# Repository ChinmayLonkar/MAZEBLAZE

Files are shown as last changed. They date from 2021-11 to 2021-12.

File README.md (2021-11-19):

# MAZEBLAZE

This repository contains hardware design files for the MAZEBLAZE Bot.This project is in developement and is not ready for final release.

It uses -
* TRCT5000 IR Sensors for following the lines on the maze 
* TB6612FNG Motor Driver for controlling two N20 motors
* ESP32 for control and perform tasks at high speeds and accuracy

Following are some images of the PCB Design

* Top View
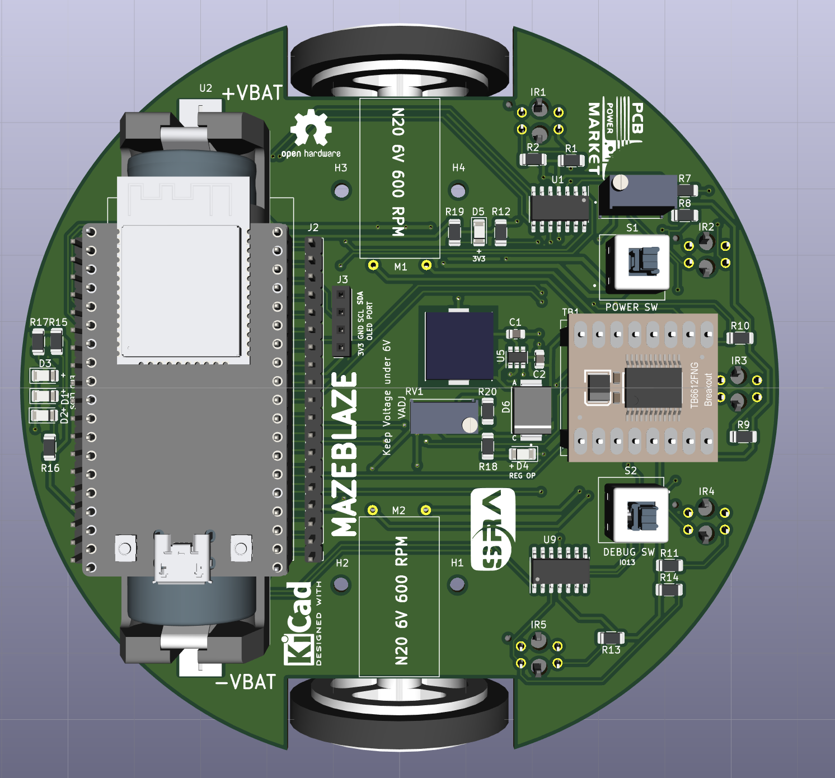
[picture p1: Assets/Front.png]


* Bottom View

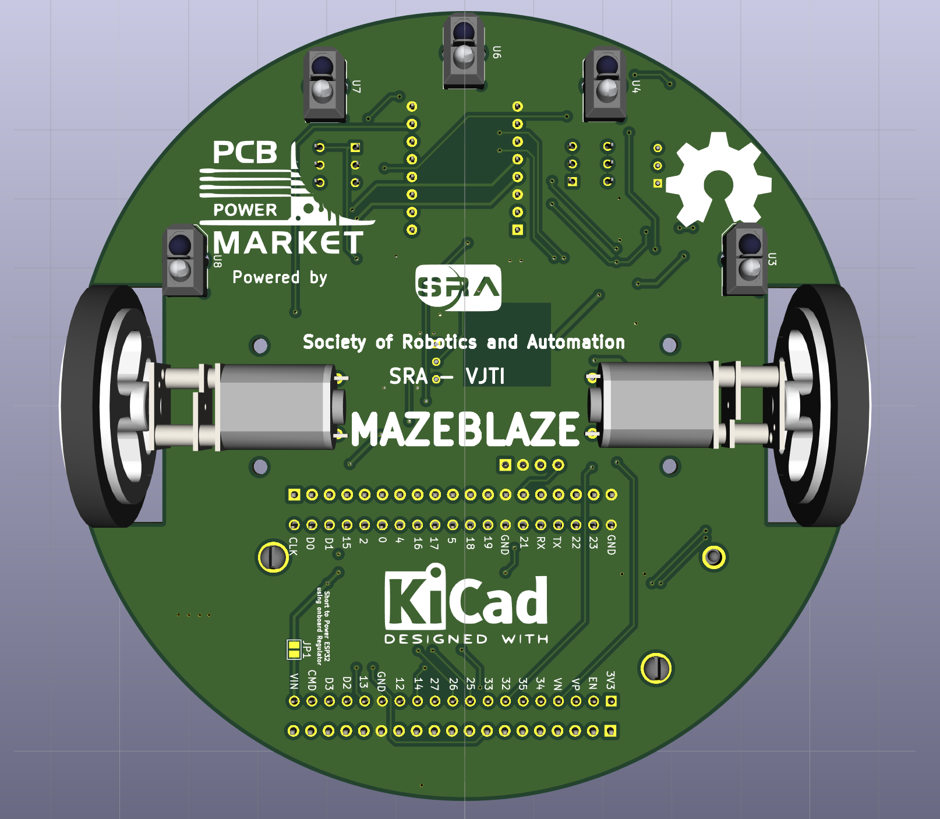
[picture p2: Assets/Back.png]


* Front Copper Layer

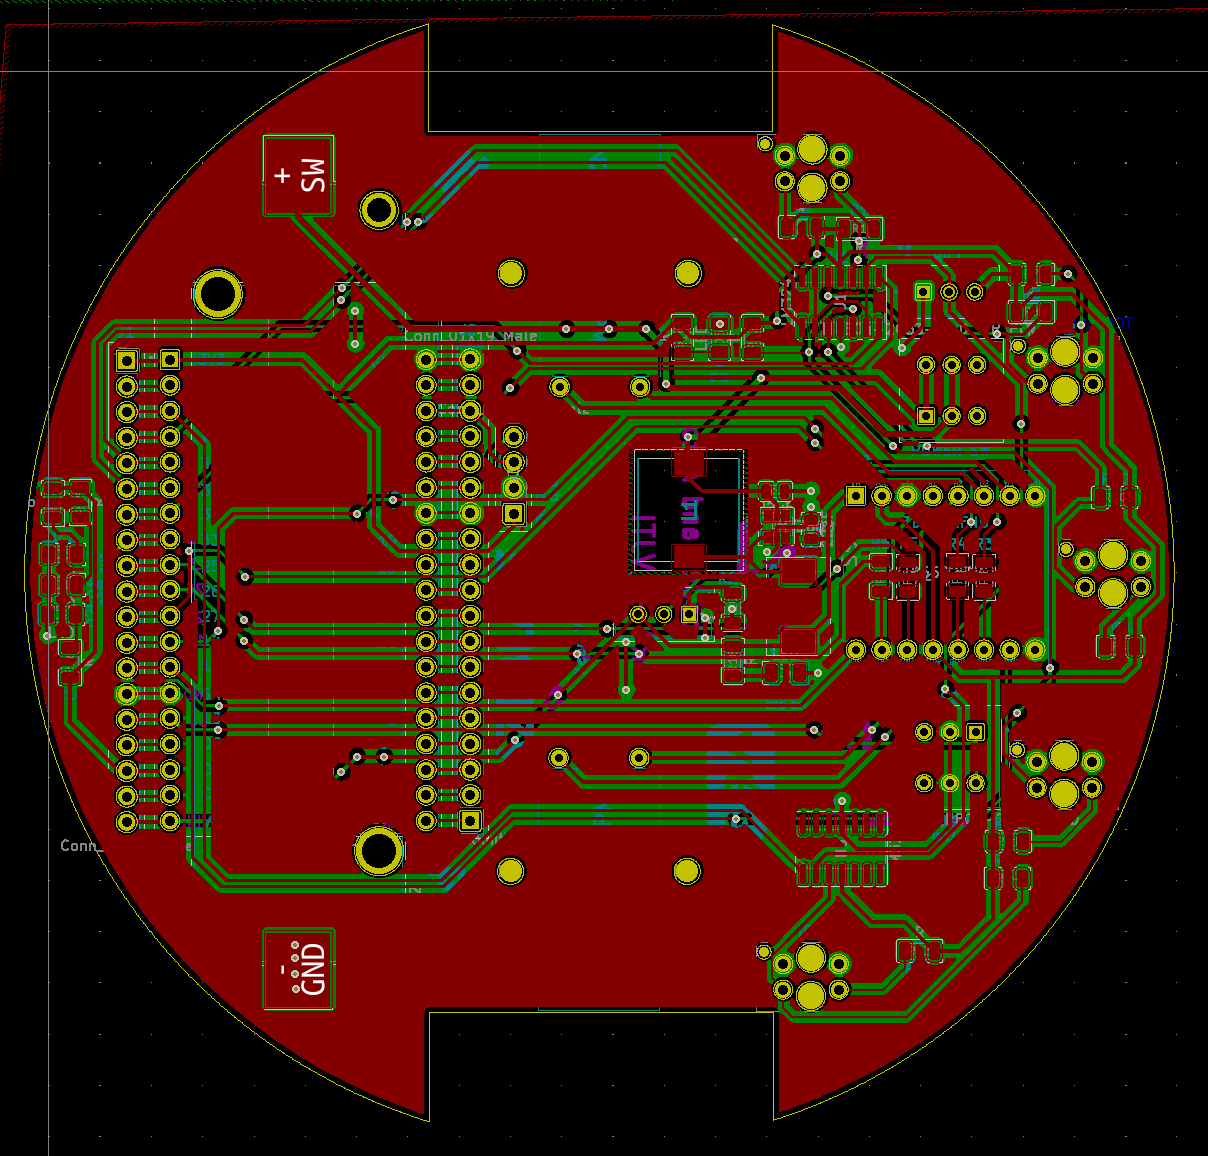
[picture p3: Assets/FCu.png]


* Bottom Copper Layer

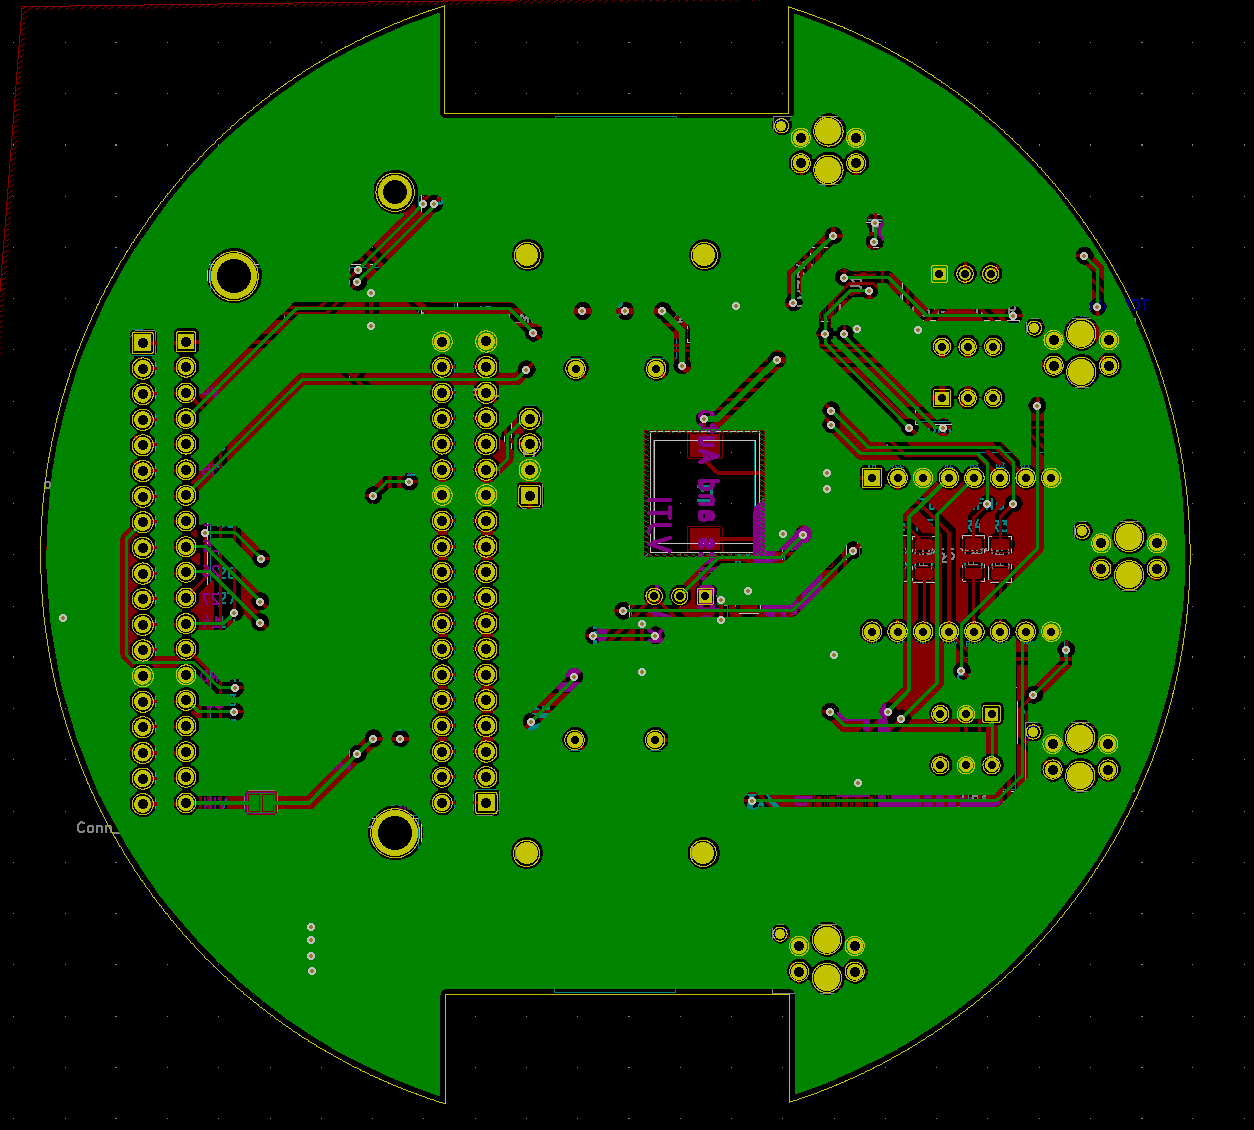
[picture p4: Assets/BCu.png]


* Routing 

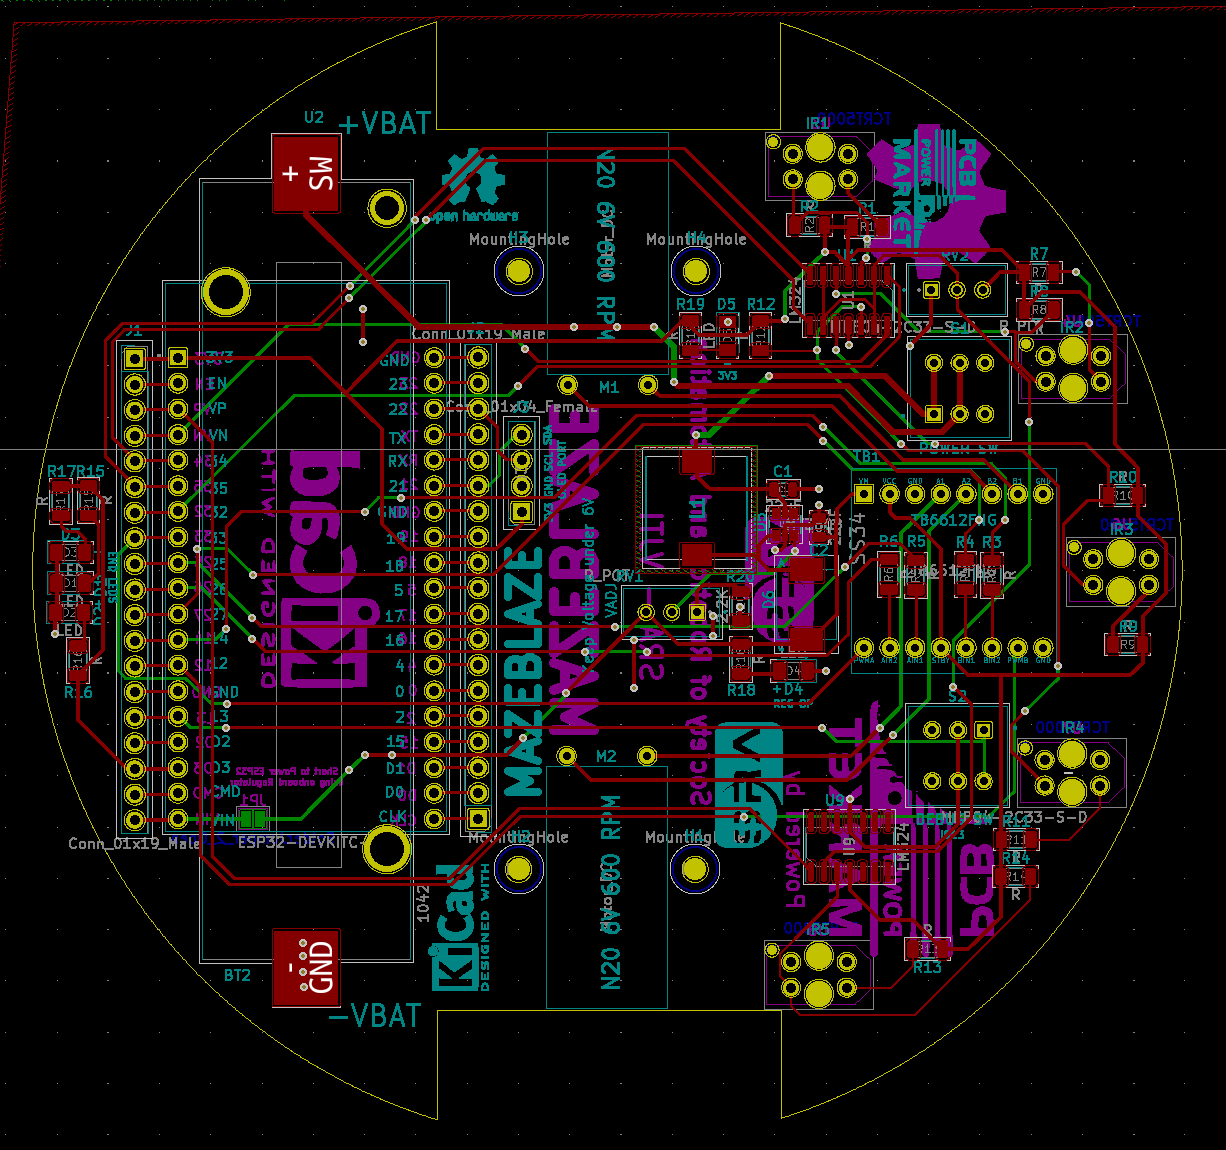
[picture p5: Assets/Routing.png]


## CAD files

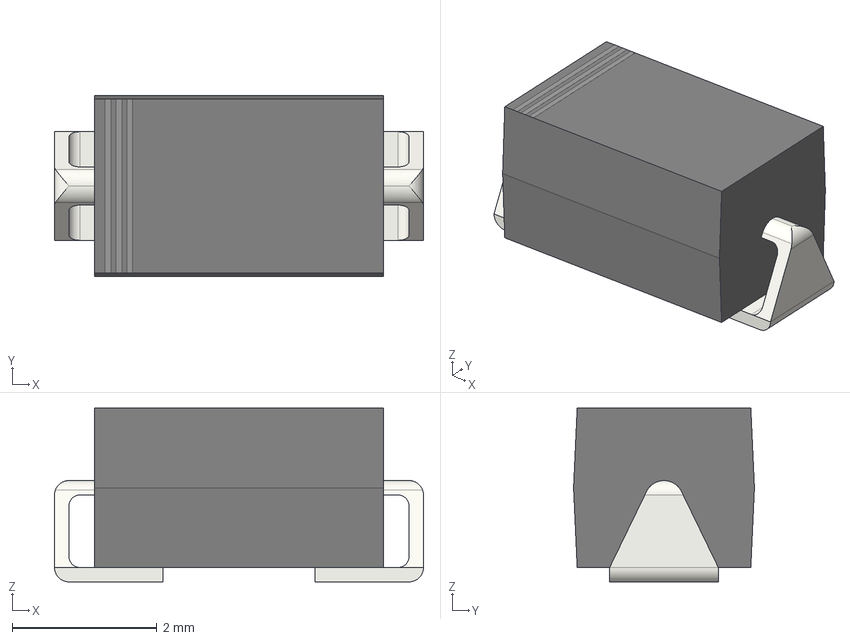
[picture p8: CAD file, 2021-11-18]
pcb_design/3D_Files/SS34.step
5.10 x 2.50 x 2.40 mm

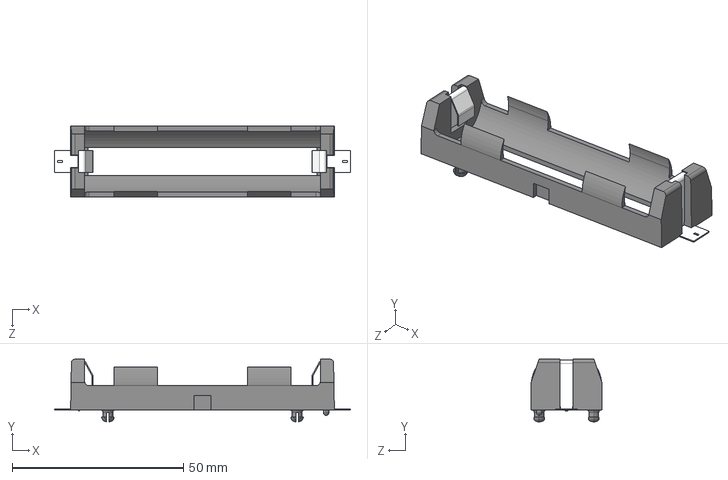
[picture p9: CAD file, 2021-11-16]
pcb_design/Component_libraries/1042/1042.step
86.5 x 18.3 x 20.7 mm

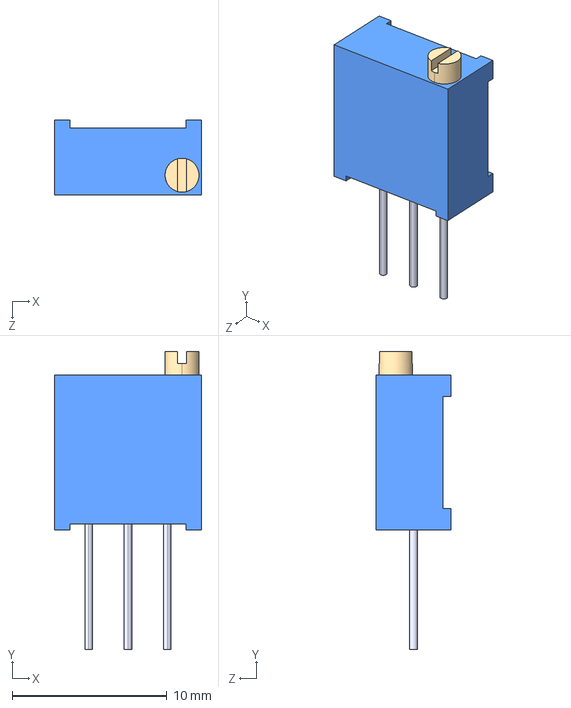
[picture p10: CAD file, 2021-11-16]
pcb_design/Component_libraries/3296W-1-202LF/3296W-1-202LF.step
9.53 x 19.3 x 4.83 mm

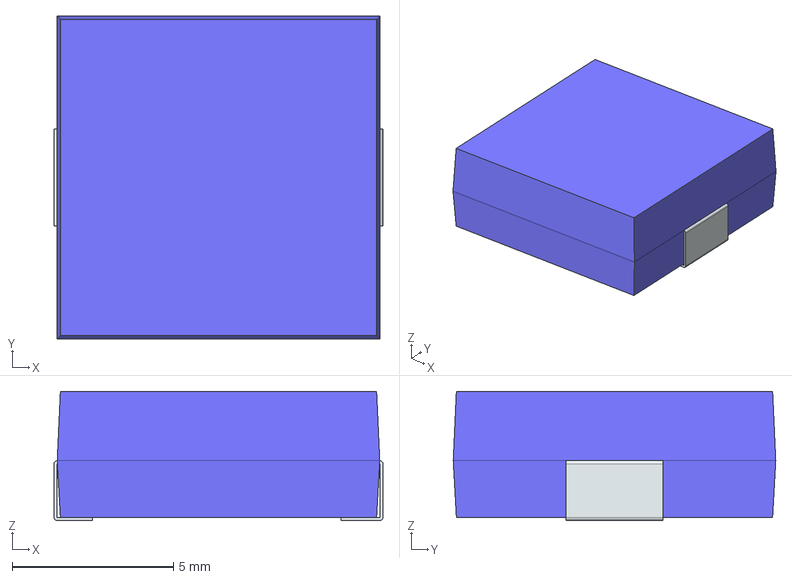
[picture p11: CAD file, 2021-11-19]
pcb_design/Component_libraries/Inductor_CDRH104RNP-220NC/CDRH104RNP-220NC.stp
10.2 x 10.0 x 4.00 mm
FilletPin1
FilletPin2

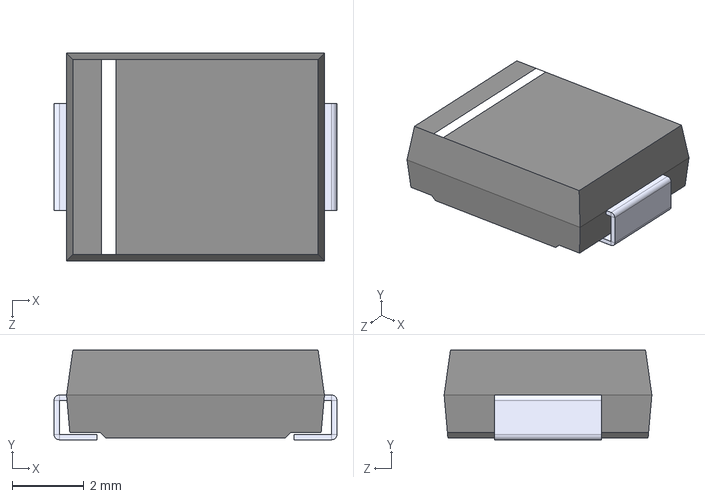
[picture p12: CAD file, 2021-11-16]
pcb_design/Component_libraries/SS34/SS34.step
7.90 x 2.50 x 5.80 mm

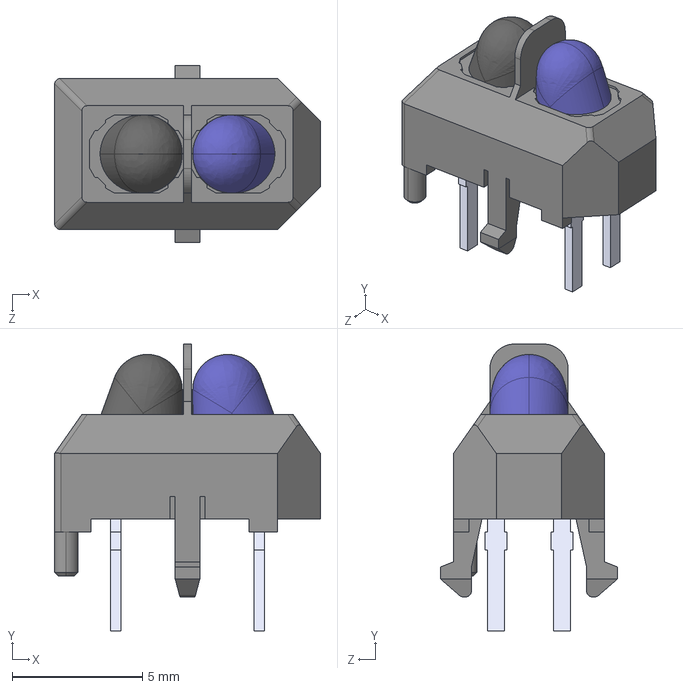
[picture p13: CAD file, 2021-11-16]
pcb_design/Component_libraries/TCRT5000/TCRT5000.step
10.2 x 11.0 x 6.80 mm

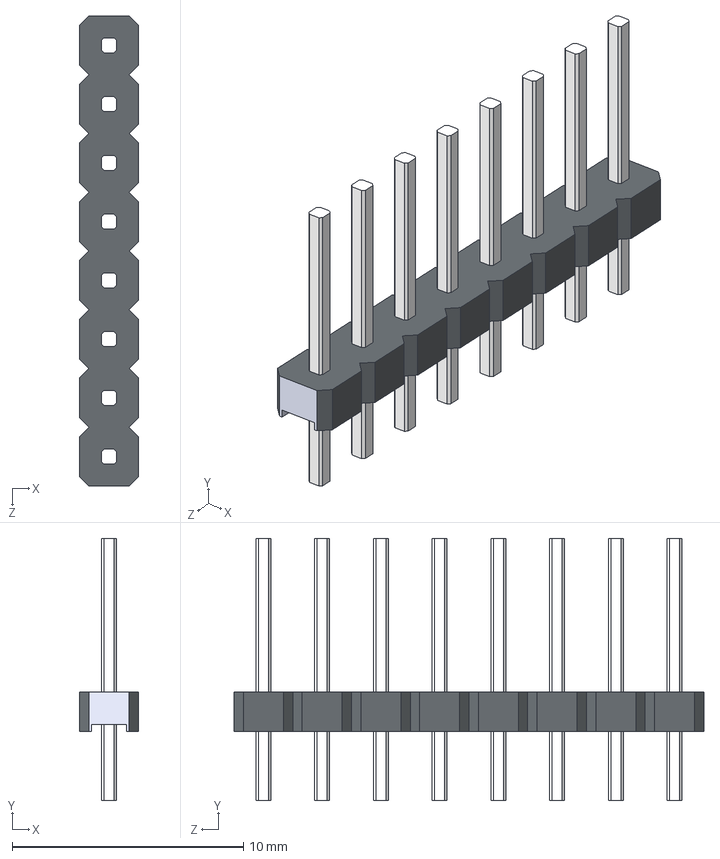
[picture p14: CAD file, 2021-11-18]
pcb_design/3D_Files/1x8.STEP
2.54 x 11.3 x 20.3 mm

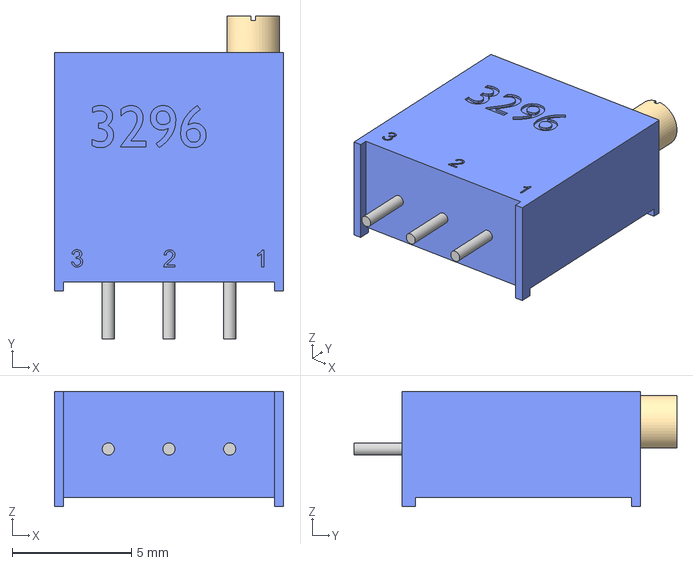
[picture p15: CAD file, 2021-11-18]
pcb_design/3D_Files/Trimpot 3296W.step
9.60 x 13.5 x 4.82 mm

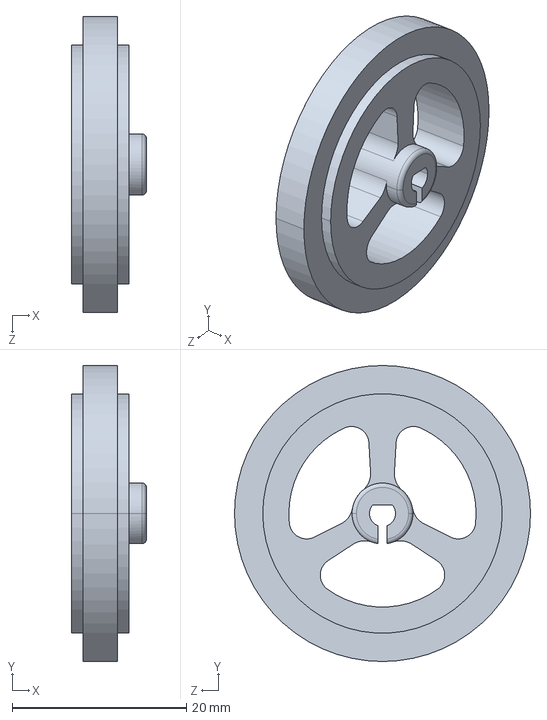
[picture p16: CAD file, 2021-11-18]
pcb_design/3D_Files/Wheel 34 mm.STEP
8.60 x 34.0 x 34.0 mm

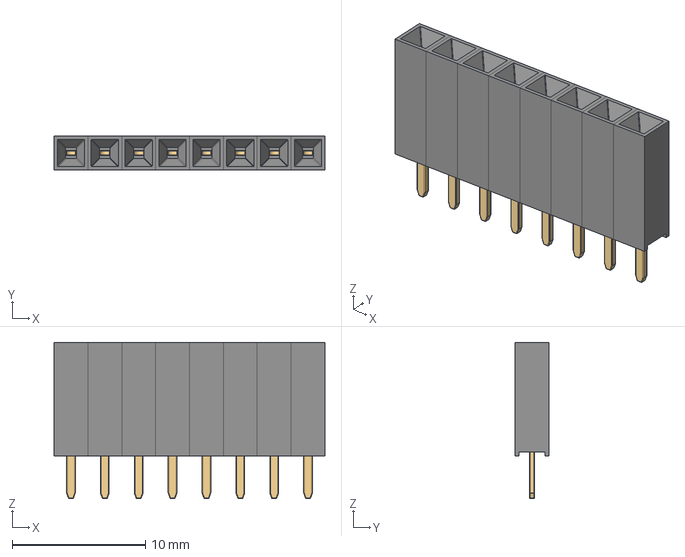
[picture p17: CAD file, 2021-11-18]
pcb_design/3D_Files/Female Pin Header 01x08 Pitch 2.54mm Height 8.5mm.stp
20.3 x 2.54 x 11.7 mm
Female Pin Header 1x x 8

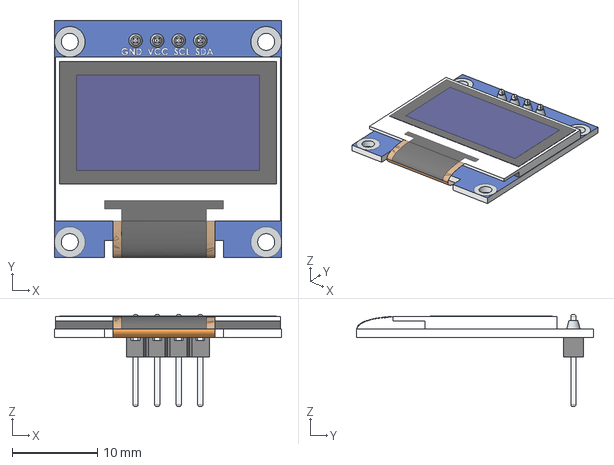
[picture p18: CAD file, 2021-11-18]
pcb_design/3D_Files/OLED-128x64-0.96.step
26.7 x 27.9 x 10.8 mm

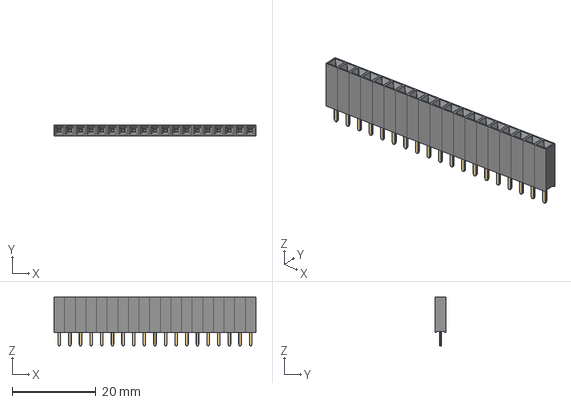
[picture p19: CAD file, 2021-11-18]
pcb_design/3D_Files/Female Pin Header 01x19 Pitch 2.54mm Height 8.5mm.stp
48.3 x 2.54 x 11.7 mm
Female Pin Header 1x x 19

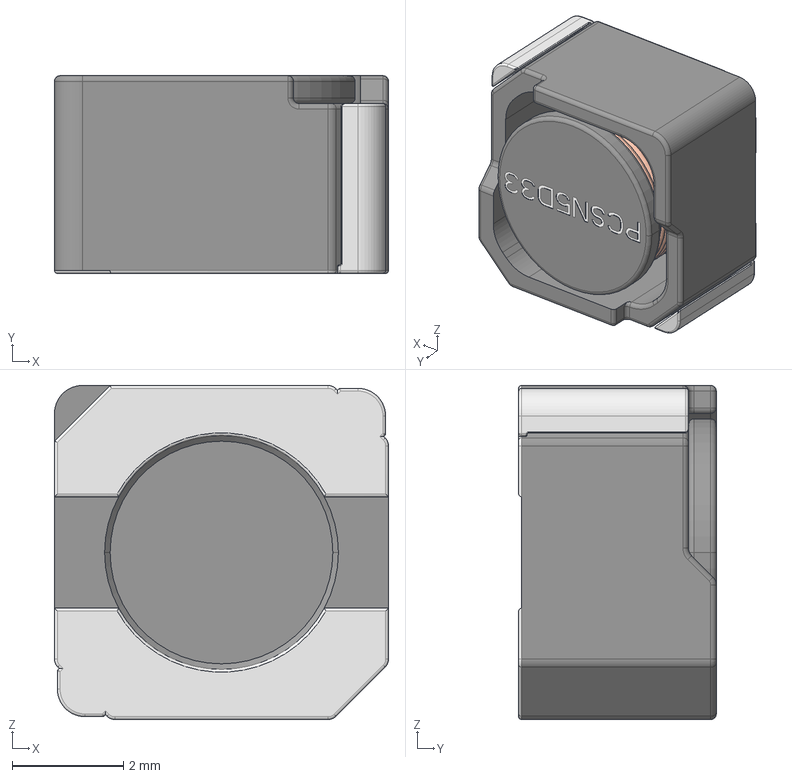
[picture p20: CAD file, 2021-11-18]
pcb_design/3D_Files/pcsn5d33_l6_w6_h3-5.stp
6.00 x 3.55 x 6.00 mm

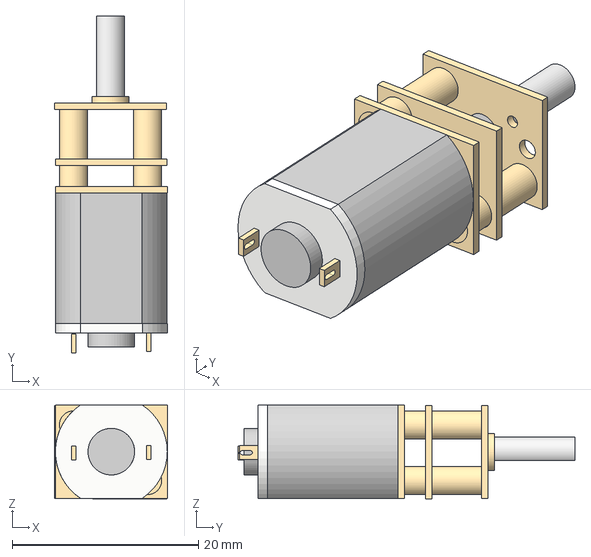
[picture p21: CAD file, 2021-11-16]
pcb_design/3D_Files/MicroGearmotor v3.step
12.1 x 36.1 x 10.1 mm

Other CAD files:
pcb_design/3D_Files/Roda 34 mm.STEP
pcb_design/3D_Files/Push Switch_8x8_6pin_with Lock.stp
pcb_design/3D_Files/18650 _87_89 0=_4.STEP
pcb_design/Component_libraries/Inductor_CDRH104RNP-220NC/CDRH104RNP-220NC.stl

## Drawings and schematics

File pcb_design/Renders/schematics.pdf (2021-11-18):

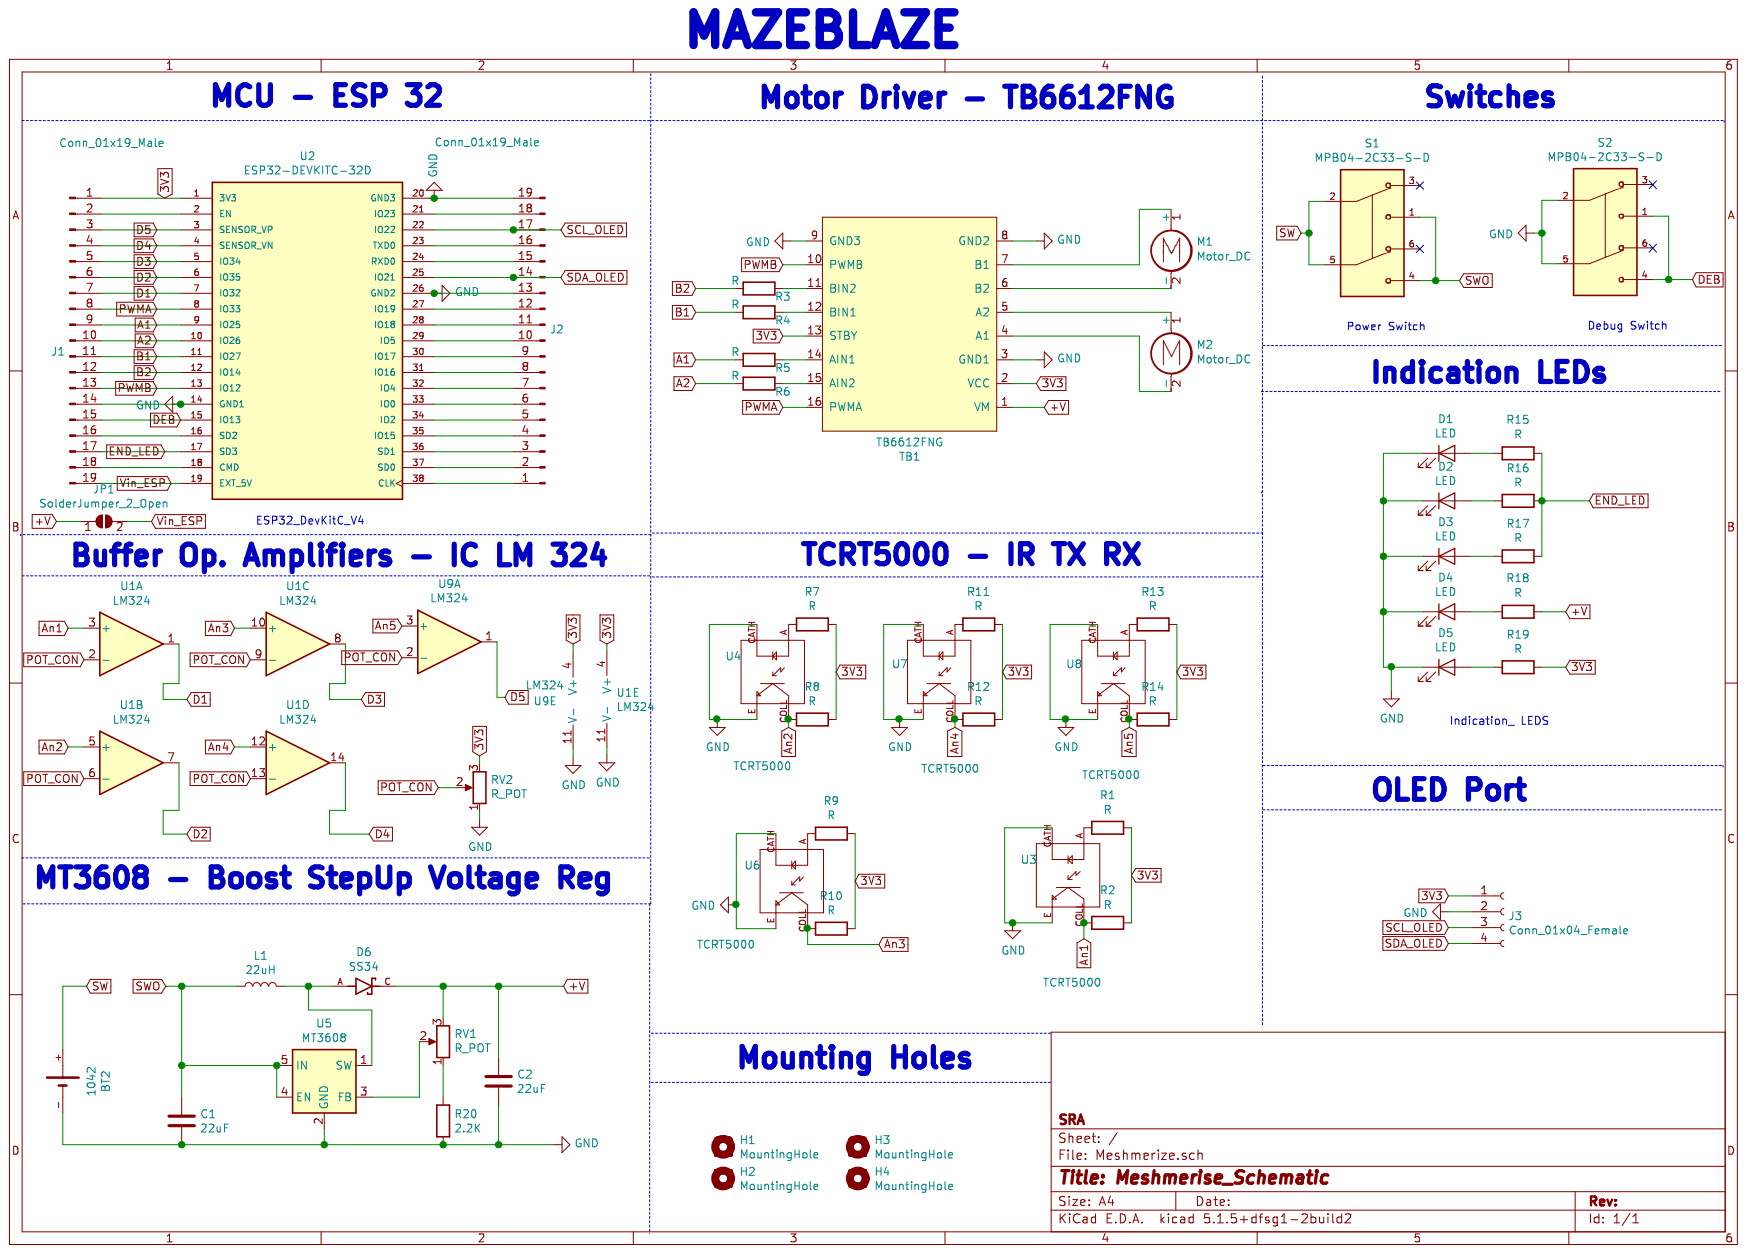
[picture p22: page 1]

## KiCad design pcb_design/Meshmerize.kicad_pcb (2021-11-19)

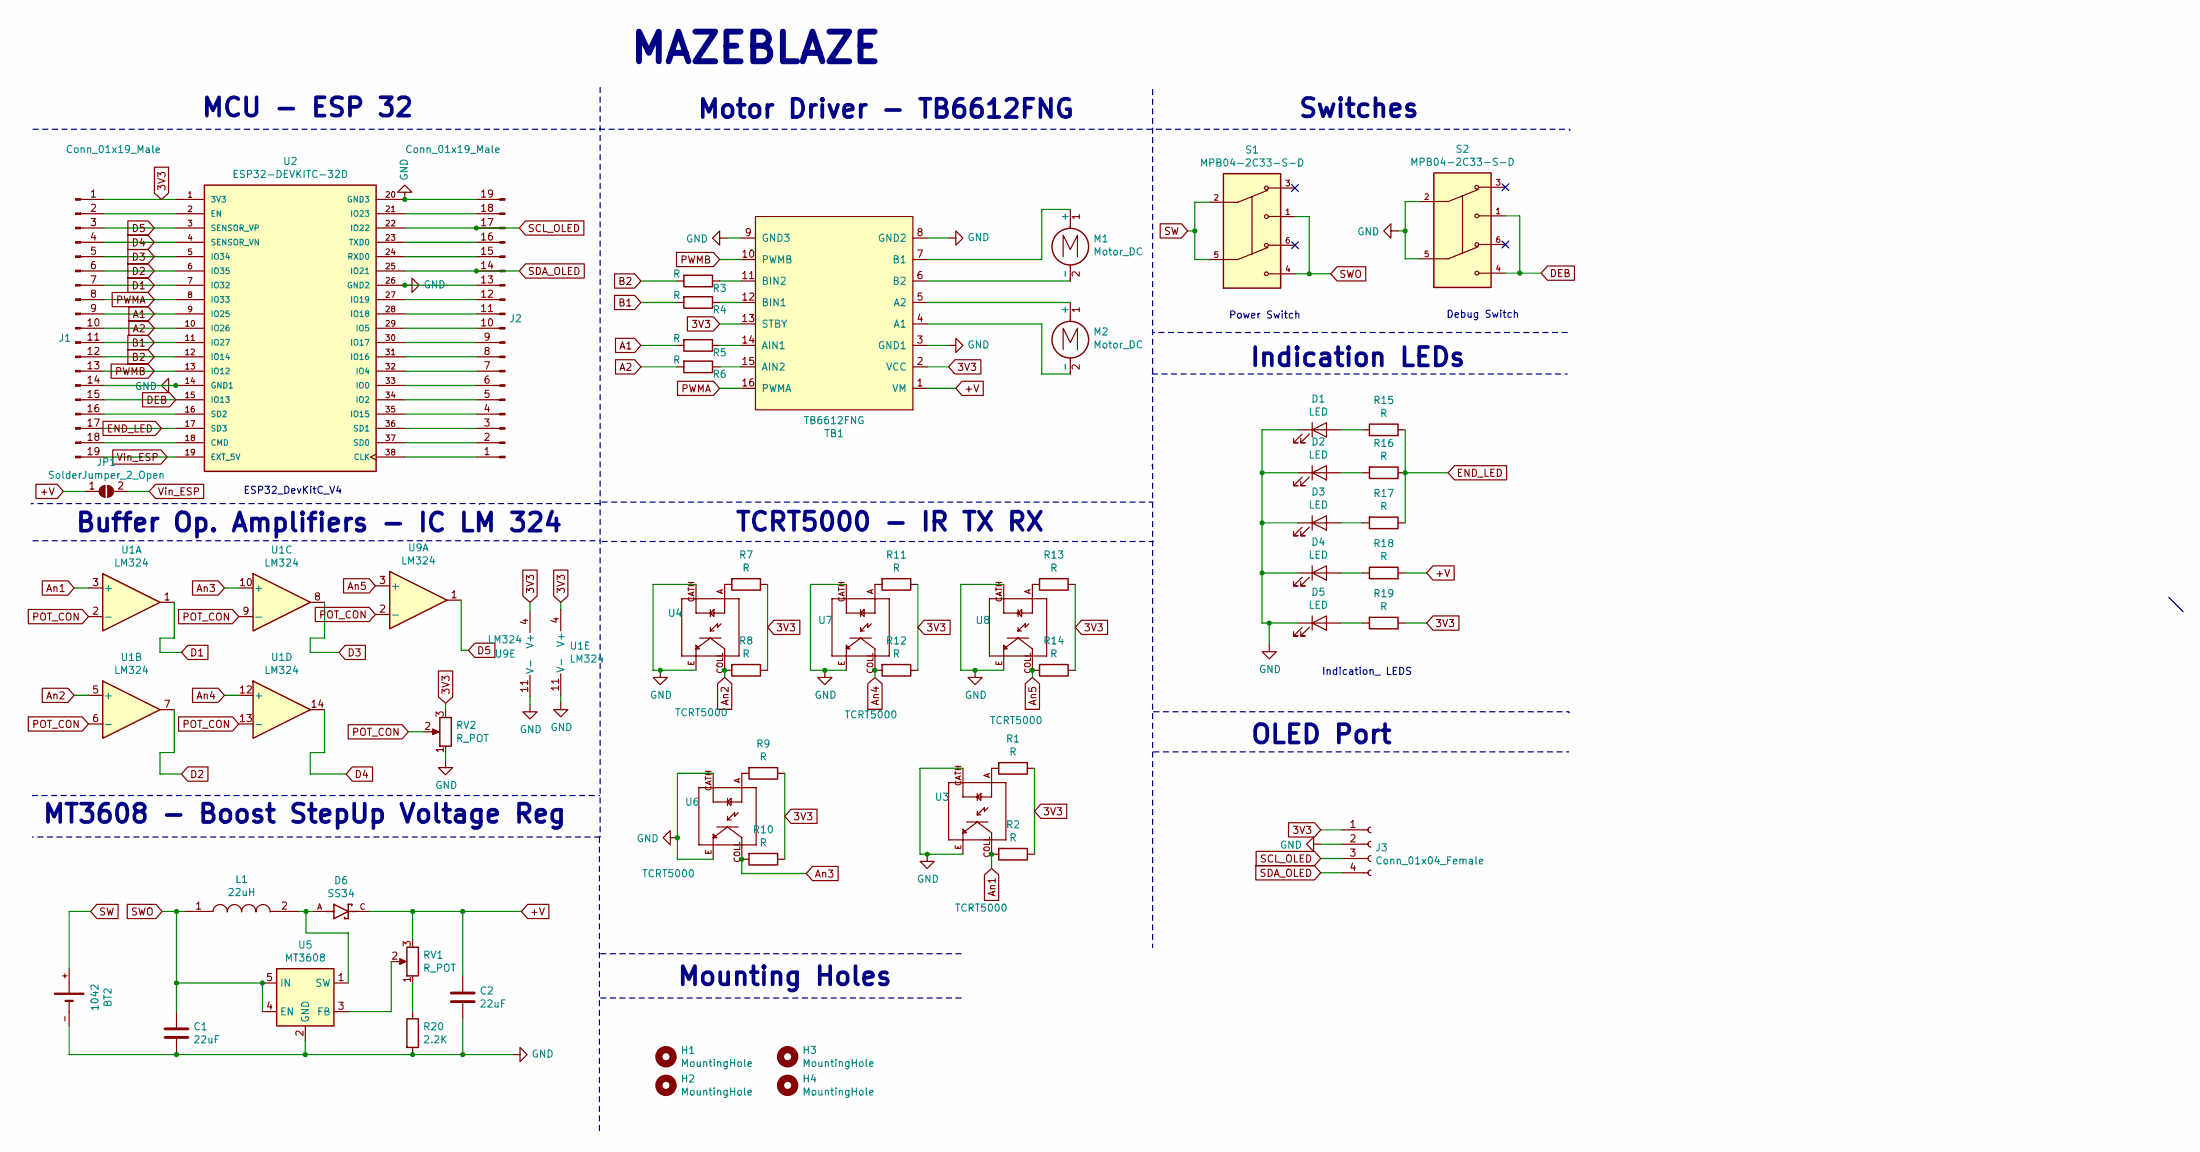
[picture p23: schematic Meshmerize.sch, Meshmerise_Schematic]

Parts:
BT2: 1042; BAT_1042
C1, C2: 22uF; C_0805_2012Metric
D1, D2, D3, D4, D5: LED; LED_1206_3216Metric
D6: SS34; DIOM7959X265N; PARTREV 31 Aug 2016
H1, H2, H3, H4: MountingHole; MountingHole_2.2mm_M2
J1, J2: Conn_01x19_Male; PinHeader_1x19_P2.54mm_Vertical
J3: Conn_01x04_Female; PinSocket_1x04_P2.54mm_Vertical
JP1: SolderJumper_2_Open; SolderJumper-2_P1.3mm_Open_Pad1.0x1.5mm
L1: 22uH; INDPM102100X400N; Manufacturer_Part_Number CDRH104RNP-220NC; Mouser Part Number 851-CDRH104RNP-220NC
M1, M2: Motor_DC; N20_Motor
R1, R2, R3, R4, R5, R6, R7, R8, R9, R10, R11, R12, R13, R14, R15, R16, R17, R18, R19: R; R_1206_3216Metric
R20: 2.2K; R_1206_3216Metric
RV1, RV2: R_POT; TRIM_3296W-1-202LF
S1, S2: MPB04-2C33-S-D; SW_MPB04-2C33-S-D; PARTREV 1.0
TB1: TB6612FNG
U1, U9: LM324; SOIC-14_3.9x8.7mm_P1.27mm
U2: ESP32-DEVKITC-32D; MODULE_ESP32-DEVKITC-32D; PARTREV 4
U3, U4, U6, U7, U8: TCRT5000; OPTO_TCRT5000; PARTREV 1.7
U5: MT3608; SOT-23-6

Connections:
3V3: J1.1, J3.1, R1.1, R2.1, R7.1, R8.1, R9.1, R10.1, R11.1, R12.1, R13.1, R14.1, R19.1, RV2.3, TB1.2 (VCC), TB1.13 (STBY), U1.4 (V+), U2.1 (3V3), U9.4 (V+)
+V: C2.1, D6.C, JP1.1 (A), R18.2, RV1.3, TB1.1 (VM)
A1: J1.9, R5.2, U2.9 (IO25)
A2: J1.10, R6.2, U2.10 (IO26)
An1: R2.2, U1.3 (+), U3.COLL
An2: R8.2, U1.5 (+), U4.COLL
An3: R10.2, U1.10 (+), U6.COLL
An4: R12.2, U1.12 (+), U7.COLL
An5: R14.2, U8.COLL, U9.3 (+)
B1: J1.11, R4.2, U2.11 (IO27)
B2: J1.12, R3.2, U2.12 (IO14)
D1: J1.7, U1.1, U2.7 (IO32)
D2: J1.6, U1.7, U2.6 (IO35)
D3: J1.5, U1.8, U2.5 (IO34)
D4: J1.4, U1.14, U2.4 (SENSOR_VN)
D5: J1.3, U2.3 (SENSOR_VP), U9.1
DEB: J1.15, S2.1, S2.4, U2.15 (IO13)
END_LED: J1.17, R15.2, R16.1, R17.1, U2.17 (SD3)
GND: BT2.-, C1.2, C2.2, D1.1 (K), D2.1 (K), D3.1 (K), D4.1 (K), D5.1 (K), J1.14, J2.13, J2.19, J3.2, R20.2, RV2.1, S2.2, S2.5, TB1.3 (GND1), TB1.8 (GND2), TB1.9 (GND3), U1.11 (V-), U2.14 (GND1), U2.20 (GND3), U2.26 (GND2), U3.CATH, U3.E, U4.CATH, U4.E, U5.2 (GND), U6.CATH, U6.E, U7.CATH, U7.E, U8.CATH, U8.E, U9.11 (V-)
unnamed: D1.2 (A), R15.1
unnamed: D2.2 (A), R16.2
unnamed: D3.2 (A), R17.2
unnamed: D4.2 (A), R18.1
unnamed: D5.2 (A), R19.2
unnamed: D6.A, L1.2, U5.1 (SW)
unnamed: J1.2, U2.2 (EN)
unnamed: J1.16, U2.16 (SD2)
unnamed: J1.18, U2.18 (CMD)
unnamed: J2.1, U2.38 (CLK)
unnamed: J2.2, U2.37 (SD0)
unnamed: J2.3, U2.36 (SD1)
unnamed: J2.4, U2.35 (IO15)
unnamed: J2.5, U2.34 (IO2)
unnamed: J2.6, U2.33 (IO0)
unnamed: J2.7, U2.32 (IO4)
unnamed: J2.8, U2.31 (IO16)
unnamed: J2.9, U2.30 (IO17)
unnamed: J2.10, U2.29 (IO5)
unnamed: J2.11, U2.28 (IO18)
unnamed: J2.12, U2.27 (IO19)
unnamed: J2.15, U2.24 (RXD0)
unnamed: J2.16, U2.23 (TXD0)
unnamed: J2.18, U2.21 (IO23)
unnamed: M1.1 (+), TB1.7 (B1)
unnamed: M1.2 (-), TB1.6 (B2)
unnamed: M2.1 (+), TB1.5 (A2)
unnamed: M2.2 (-), TB1.4 (A1)
unnamed: R1.2, U3.A
unnamed: R3.1, TB1.11 (BIN2)
unnamed: R4.1, TB1.12 (BIN1)
unnamed: R5.1, TB1.14 (AIN1)
unnamed: R6.1, TB1.15 (AIN2)
unnamed: R7.2, U4.A
unnamed: R9.2, U6.A
unnamed: R11.2, U7.A
unnamed: R13.2, U8.A
unnamed: R20.1, RV1.1
unnamed: RV1.2, U5.3 (FB)
POT_CON: RV2.2, U1.2 (-), U1.6 (-), U1.9 (-), U1.13 (-), U9.2 (-)
PWMA: J1.8, TB1.16 (PWMA), U2.8 (IO33)
PWMB: J1.13, TB1.10 (PWMB), U2.13 (IO12)
SCL_OLED: J2.17, J3.3, U2.22 (IO22)
SDA_OLED: J2.14, J3.4, U2.25 (IO21)
SW: BT2.+, S1.2, S1.5
SWO: C1.1, L1.1, S1.1, S1.4, U5.4 (EN), U5.5 (IN)
Vin_ESP: J1.19, JP1.2 (B), U2.19 (EXT_5V)

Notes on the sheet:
Indication_ LEDS
ESP32_DevKitC_V4
MAZEBLAZE
MCU - ESP 32
Motor Driver - TB6612FNG
Switches
Debug Switch
Power Switch
Buffer Op. Amplifiers - IC LM 324
TCRT5000 - IR TX RX
MT3608 - Boost StepUp Voltage Reg
Mounting Holes
Indication LEDs
OLED Port

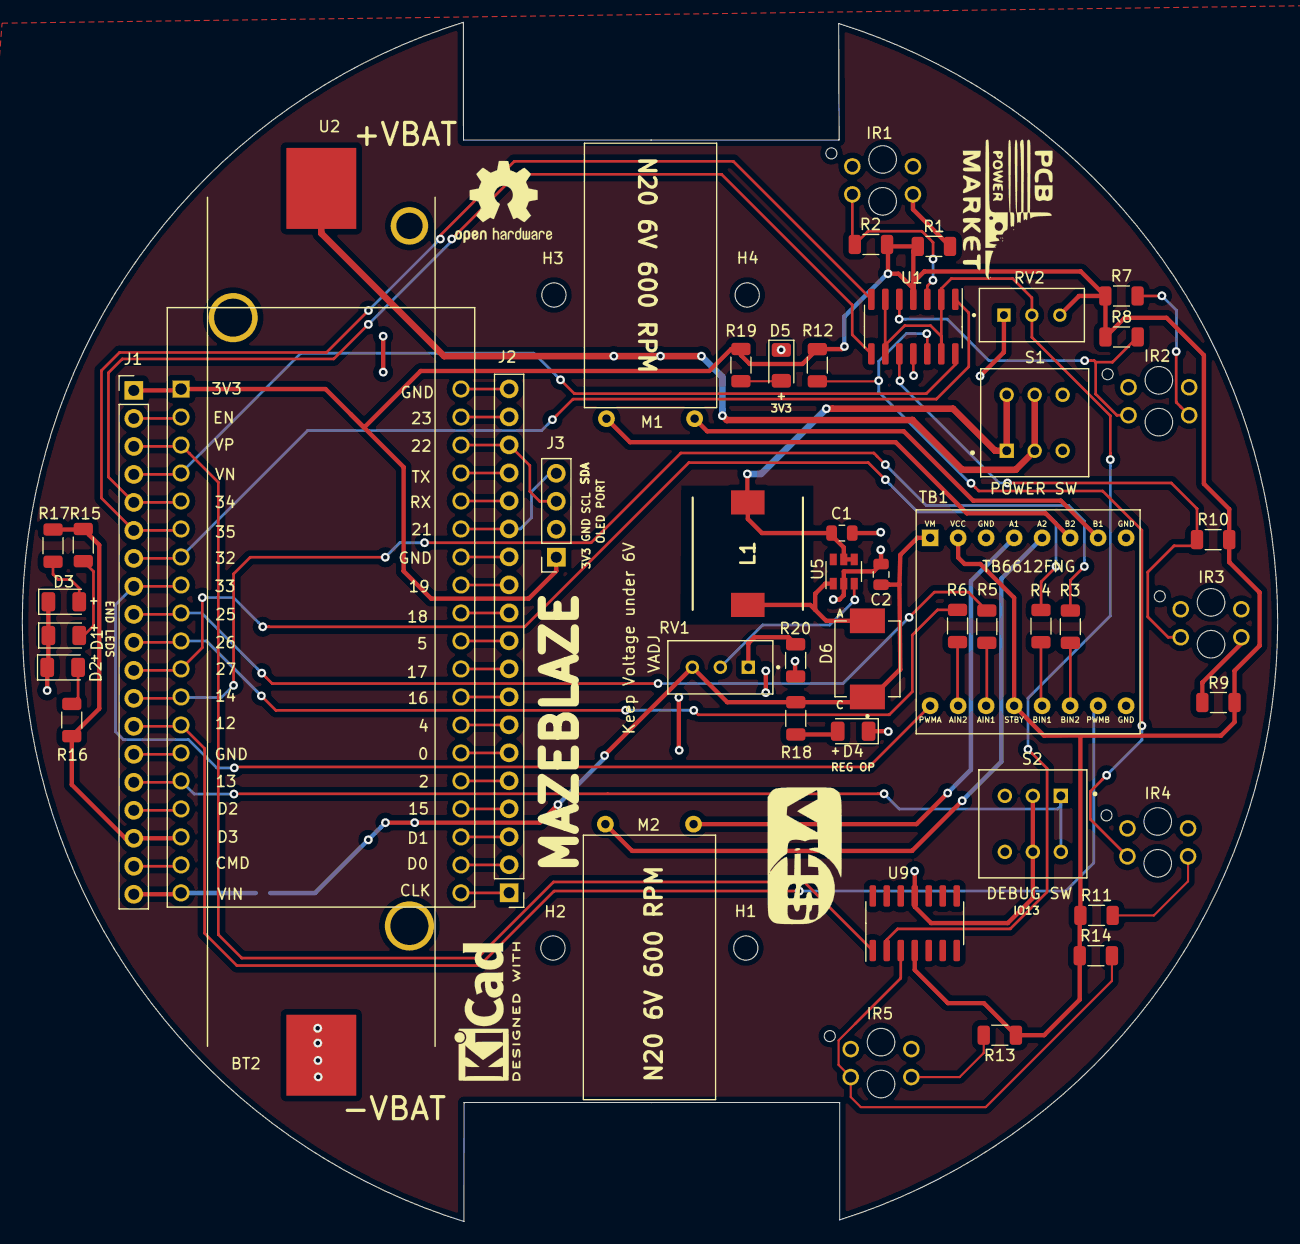
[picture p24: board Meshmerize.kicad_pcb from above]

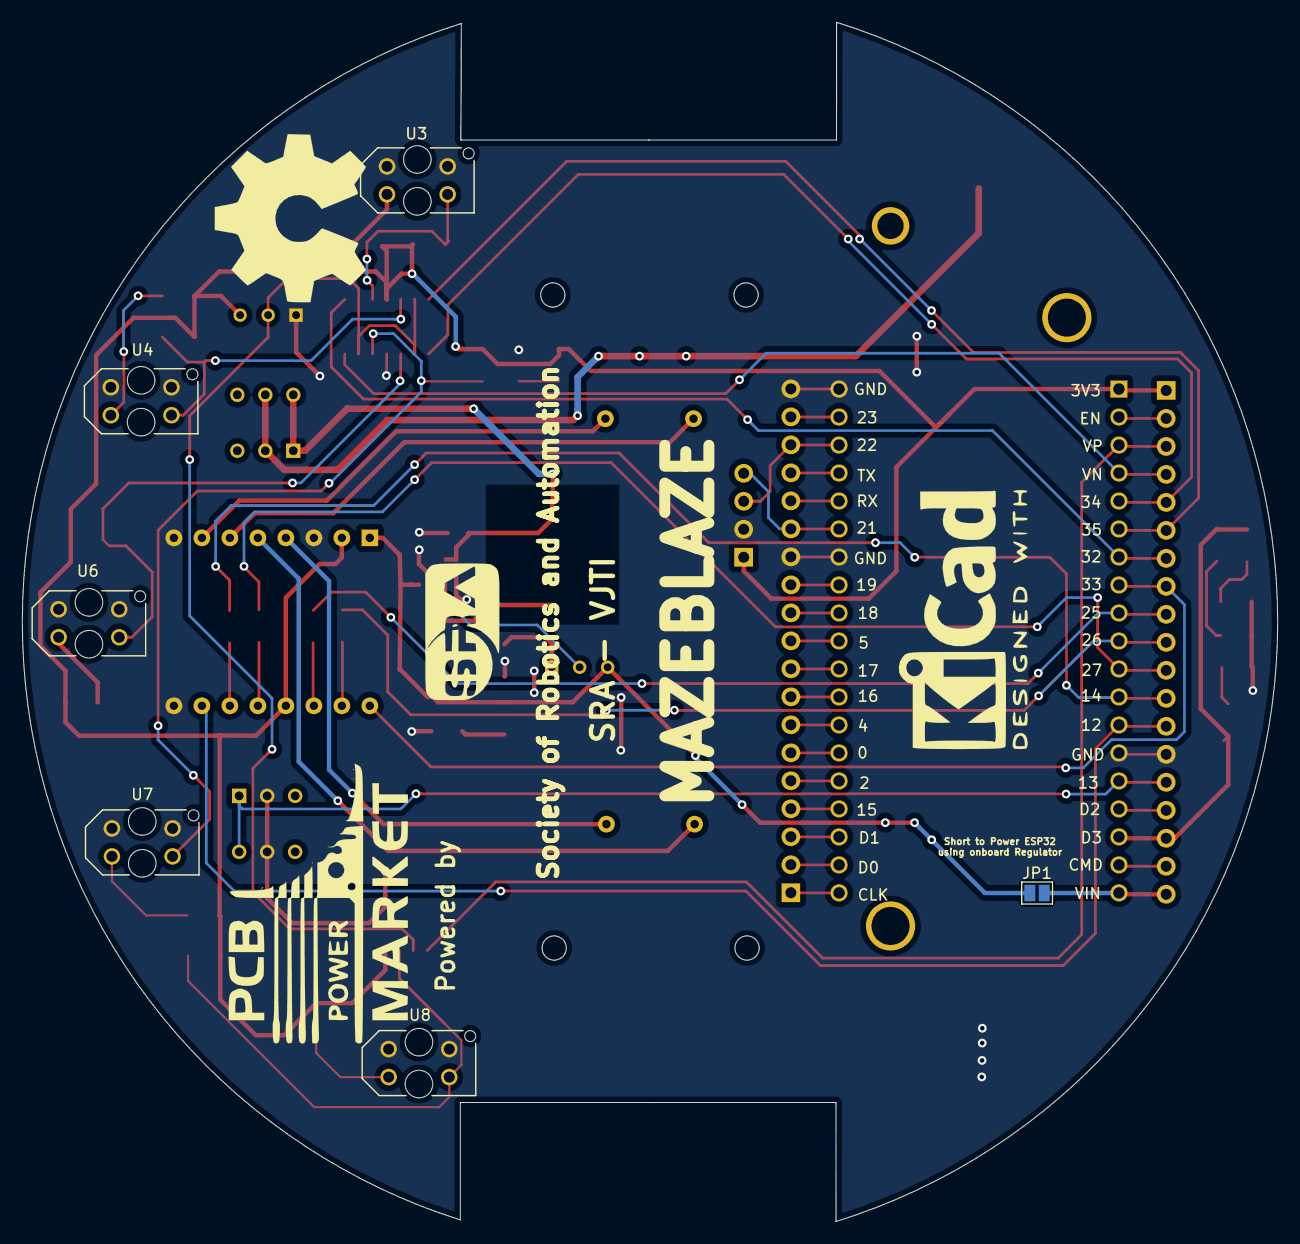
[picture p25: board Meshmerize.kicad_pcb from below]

Board: 2 copper layers, 113.9 x 108.8 mm, 54 parts (6 on the bottom side), 66 nets.

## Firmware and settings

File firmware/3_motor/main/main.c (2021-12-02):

#include "mazeblaze.h"

void app_main(void)
{
    ESP_ERROR_CHECK(enable_lsa());
    ESP_ERROR_CHECK(enable_motor_driver());

    while (1)
    {
        printf("%d %d %d %d %d \n", read_lsa().lsa_read[0], read_lsa().lsa_read[2], read_lsa().lsa_read[1], read_lsa().lsa_read[4], read_lsa().lsa_read[3]);
        if (read_lsa().lsa_read[1] == 100)
        {
            set_motor_speed(MOTOR_A_0, MOTOR_FORWARD, 80);
            set_motor_speed(MOTOR_A_1, MOTOR_FORWARD, 80);
            vTaskDelay(100 / portTICK_RATE_MS);
            // set_motor_speed(MOTOR_A_1, MOTOR_FORWARD, 100);
            // set_motor_speed(MOTOR_A_0, MOTOR_BACKWARD, 100);
            // vTaskDelay(1000/portTICK_RATE_MS);
            // set_motor_speed(MOTOR_A_0, MOTOR_STOP, 100);
            // set_motor_speed(MOTOR_A_1, MOTOR_STOP, 100);
            // vTaskDelay(1000/portTICK_RATE_MS);
        }
        else if (read_lsa().lsa_read[0] == 100)
        {
            set_motor_speed(MOTOR_A_0, MOTOR_BACKWARD, 80);
            set_motor_speed(MOTOR_A_1, MOTOR_FORWARD, 80);
            vTaskDelay(60 / portTICK_RATE_MS);
            // set_motor_speed(MOTOR_A_1, MOTOR_FORWARD, 100);
            // set_motor_speed(MOTOR_A_0, MOTOR_BACKWARD, 100);
            // vTaskDelay(1000/portTICK_RATE_MS);
            // set_motor_speed(MOTOR_A_0, MOTOR_STOP, 100);
            // set_motor_speed(MOTOR_A_1, MOTOR_STOP, 100);
            // vTaskDelay(1000/portTICK_RATE_MS);
        }
        if (read_lsa().lsa_read[3] == 100)
        {
            set_motor_speed(MOTOR_A_0, MOTOR_FORWARD, 80);
            set_motor_speed(MOTOR_A_1, MOTOR_BACKWARD, 80);
            vTaskDelay(60 / portTICK_RATE_MS);
            // set_motor_speed(MOTOR_A_1, MOTOR_FORWARD, 100);
            // set_motor_speed(MOTOR_A_0, MOTOR_BACKWARD, 100);
            // vTaskDelay(1000/portTICK_RATE_MS);
            // set_motor_speed(MOTOR_A_0, MOTOR_STOP, 100);
            // set_motor_speed(MOTOR_A_1, MOTOR_STOP, 100);
            // vTaskDelay(1000/portTICK_RATE_MS);
        }
        // else{
        //     set_motor_speed(MOTOR_A_0, MOTOR_STOP, 0);
        //     set_motor_speed(MOTOR_A_1, MOTOR_STOP, 0);
        // }

        vTaskDelay(100/ portTICK_RATE_MS);
}
}

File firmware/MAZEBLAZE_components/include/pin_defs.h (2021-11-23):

#ifndef PIN_DEFS_H
#define PIN_DEFS_H

#define CHECK(x)                \
    do                          \
    {                           \
        esp_err_t __;           \
        if ((__ = x) != ESP_OK) \
            return __;          \
    } while (0)
#define CHECK_LOGE(err, x, tag, msg, ...)      \
    do                                         \
    {                                          \
        if ((err = x) != ESP_OK)               \
        {                                      \
            ESP_LOGE(tag, msg, ##__VA_ARGS__); \
            return err;                        \
        }                                      \
    } while (0)



#define END_LED 10

#define DEBUG_SWITCH 13


#define LSA_D0 32
#define LSA_D1 35
#define LSA_D2 34
#define LSA_D3 39
#define LSA_D4 36

#define SCL_OLED 22
#define SDA_OLED 21

/////// motor driver ////////
//****** normal mode ******//
#define PWM_A 33 //MCPWM_UNIT_1 MCPWM0A
#define AIN_1 25 //MCPWM_UNIT_1 MCPWM0B
#define AIN_2 26 //MCPWM_UNIT_1 MCPWM1A
#define PWM_B 12 //MCPWM_UNIT_1 MCPWM1B
#define BIN_1 27 //MCPWM_UNIT_1 MCPWM2A
#define BIN_2 14 //MCPWM_UNIT_1 MCPWM2B

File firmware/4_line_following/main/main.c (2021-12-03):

#include "mazeblaze.h"
#include "tuning_http_server.h"
#include "line_following.h"
#include "node_detection.h"
#include "turn.h"
#include "esp_err.h"
#include "wifi_logger.h"

void maze_explore(void *arg)
{

    while (1)
    {
        if (only_straight())
        {
            go_straight();
        }
        else if (only_left())
        {
            turn(LEFT);
        }
        else if (only_right())
        {
            turn(RIGHT);
        }

        else if (plus_node())
        {
            turn(LEFT);
        }

        else if (T_node())
        {
            turn(LEFT);
        }

        else if (straight_right())
        {
            go_straight();
        }

        else if (straight_left())
        {
            turn(LEFT);
        }

        else if (deadend())
        {
            turn(UTURN);
        }

        else if (end())
        {
            stop();
            vTaskDelete(NULL);
        }

        vTaskDelay(10 / portTICK_PERIOD_MS);
    }
}

void app_main()
{
    ESP_ERROR_CHECK(enable_lsa());
    ESP_ERROR_CHECK(enable_motor_driver());
    start_wifi_logger(); // Start wifi logger
    xTaskCreate(&start_tuning_http_server,"start server",4096,NULL,1,NULL);
    xTaskCreate(&maze_explore,"maze explore",4096,NULL,1,NULL);
    
}

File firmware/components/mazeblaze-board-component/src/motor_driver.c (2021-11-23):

#include "motor_driver.h"

static const char *TAG_MOTOR_DRIVER = "motor_driver";

esp_err_t enable_motor_driver()
{
    esp_err_t err;
        CHECK_LOGE(err, mcpwm_gpio_init(MCPWM_UNIT_1, MCPWM0A, MDA_NORMAL_IN_3), TAG_MOTOR_DRIVER, "error: %s", esp_err_to_name(err));
        CHECK_LOGE(err, mcpwm_gpio_init(MCPWM_UNIT_1, MCPWM0B, MDA_NORMAL_IN_4), TAG_MOTOR_DRIVER, "error: %s", esp_err_to_name(err));
        CHECK_LOGE(err, mcpwm_gpio_init(MCPWM_UNIT_1, MCPWM1A, MDA_NORMAL_IN_5), TAG_MOTOR_DRIVER, "error: %s", esp_err_to_name(err));
        CHECK_LOGE(err, mcpwm_gpio_init(MCPWM_UNIT_1, MCPWM1B, MDA_NORMAL_IN_6), TAG_MOTOR_DRIVER, "error: %s", esp_err_to_name(err));

    mcpwm_config_t pwm_config;
    pwm_config.frequency = 20000;
    pwm_config.cmpr_a = 0;
    pwm_config.cmpr_b = 0;
    pwm_config.counter_mode = MCPWM_UP_COUNTER;
    pwm_config.duty_mode = MCPWM_DUTY_MODE_0;
    esp_err_t err1_0 = mcpwm_init(MCPWM_UNIT_1, MCPWM_TIMER_0, &pwm_config);
    esp_err_t err1_1 = mcpwm_init(MCPWM_UNIT_1, MCPWM_TIMER_1, &pwm_config);

    if (err1_0 == ESP_OK && err1_1 == ESP_OK)
    {
        ESP_LOGI(TAG_MOTOR_DRIVER, "enabled motor");
        return ESP_OK;
    }
    else
    {
        return ESP_FAIL;
    }
}



static esp_err_t set_motor_speed_helper(int direction, float duty_cycle, mcpwm_unit_t mcpwm_num, mcpwm_timer_t timer_num)
{
    if (direction == MOTOR_FORWARD)
    {
        mcpwm_set_duty(mcpwm_num, timer_num, MCPWM_OPR_A, duty_cycle);
        mcpwm_set_duty_type(mcpwm_num, timer_num, MCPWM_OPR_A, MCPWM_DUTY_MODE_0);
        mcpwm_set_duty(mcpwm_num, timer_num, MCPWM_OPR_B, 0);
        mcpwm_set_duty_type(mcpwm_num, timer_num, MCPWM_OPR_B, MCPWM_DUTY_MODE_0);

        return ESP_OK;
    }
    else if (direction == MOTOR_BACKWARD)
    {
        mcpwm_set_duty(mcpwm_num, timer_num, MCPWM_OPR_A, 0);
        mcpwm_set_duty_type(mcpwm_num, timer_num, MCPWM_OPR_A, MCPWM_DUTY_MODE_0);
        mcpwm_set_duty(mcpwm_num, timer_num, MCPWM_OPR_B, duty_cycle);
        mcpwm_set_duty_type(mcpwm_num, timer_num, MCPWM_OPR_B, MCPWM_DUTY_MODE_0);

        return ESP_OK;
    }
    else if (direction == MOTOR_STOP)
    {
        mcpwm_set_duty(mcpwm_num, timer_num, MCPWM_OPR_A, 0);
        mcpwm_set_duty_type(mcpwm_num, timer_num, MCPWM_OPR_A, MCPWM_DUTY_MODE_0);
        mcpwm_set_duty(mcpwm_num, timer_num, MCPWM_OPR_B, 0);
        mcpwm_set_duty_type(mcpwm_num, timer_num, MCPWM_OPR_B, MCPWM_DUTY_MODE_0);

        return ESP_OK;
    }
    else
    {
        ESP_LOGE(TAG_MOTOR_DRIVER, "invalid motor direction selected");
        return ESP_FAIL;
    }
}

esp_err_t set_motor_speed(int motor_id, int direction, float duty_cycle)
{
   mcpwm_timer_t timer_val = motor_id == MOTOR_A_0 ? MCPWM_TIMER_0 : MCPWM_TIMER_1;
   return set_motor_speed_helper(direction, duty_cycle, MCPWM_UNIT_1, timer_val);
}

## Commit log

2021-11-16 Added Kicad project for Meshmerize bot
    [1042.step, 3296W-1-202LF.step, Apoio Contato.ipt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]
2021-11-17 Completed PCB Routing
    [Apoio Contato.ipt, Base.ipt, Carcaça.ipt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]
2021-11-17 Changes made in footprint
    [Meshmerize.kicad_pcb]
2021-11-17 Optimized schematics, routing and performed clean up
    [Meshmerize.kicad_pcb, Meshmerize.sch]
2021-11-17 Added R-Pot for LSA sensitivity, jumper to power ESP32 using inbuilt regulator, minor optimizations
    [Meshmerize.kicad_pcb, Meshmerize.sch]
2021-11-17 Modified Silkscreen and created Gerber Files
    [Meshmerize-B_Cu.gbl, Meshmerize-B_Mask.gbs, Meshmerize-B_SilkS.gbo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]
2021-11-17 Made minor changes in Back silkscreen and front copper traces
    [Meshmerize-B_Cu.gbl, Meshmerize-B_Mask.gbs, Meshmerize-B_SilkS.gbo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]
2021-11-17 Stitched Vias for Continuous Ground Plane, minor silkscreen fixes
    [Meshmerize.kicad_pcb]
2021-11-18 Added 3D Files
    [1042.step, 18650 _87_89 0=_4.STEP, 1x8.STEP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]
2021-11-18 Added Logos
    [Meshmerize.kicad_pcb]
2021-11-18 Added silkscreen, asset images, updated renders and gerbers
    [Meshmerize-B_Cu.gbl, Meshmerize-B_Mask.gbs, Meshmerize-B_SilkS.gbo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]
2021-11-19 Fixed errors, optlized routing
    [CDRH104RNP-220NC.stl, CDRH104RNP-220NC.stp, Meshmerize.kicad_pcb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]
2021-11-19 Updated readme file and gerbers
    [Meshmerize-B_Cu.gbl, Meshmerize-B_Mask.gbs, Meshmerize-B_SilkS.gbo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]
2021-11-19 Shortened MAZEBLAZE title on B.silk
    [Meshmerize.kicad_pcb]
2021-11-19 Updated Gerbers after minor silkscreen fixes
    [Meshmerize-B_Cu.gbl, Meshmerize-B_Mask.gbs, Meshmerize-B_SilkS.gbo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]
2021-11-23 PCB design files for MAZEBLAZE bot
    [1042.step, 18650 _87_89 0=_4.STEP, 1x8.STEP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]
2021-11-23 Updated firmware with some minor fixes
    [lsa.c, main.c, motor_driver.c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]
2021-11-23 Added Motor Component
2021-11-23 Added a basic example for running motor
2021-11-26 Implement Wifi for changing PID values
2021-11-27 LSA + Motor control
2021-11-29 Changes made in motor configration as per hardware setup
2021-11-29 Made changes in motor driver component according to hardware setup
2021-11-30 Adds line_following in examples
    [partition_table.csv]
2021-12-01 Creates the mazeblaze board component
2021-12-01 Corrects the linefollwing bug
    [lsa.c, motor_driver.c, motor_driver.h]
2021-12-01 Refactores and solves minor error
    [main.c, turn.c]
2021-12-01 Code flow optimized
2021-12-02 Modified motor Algorithm
